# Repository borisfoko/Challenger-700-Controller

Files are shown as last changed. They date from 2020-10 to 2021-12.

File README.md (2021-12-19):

# Challenger-700-Controller
Dieses Projekt dient als demonstrator für den Einsatz von IoT Tracking und Zugangskontrolle Einheiten auf Flugzeugsschlepper (Challenger 700). Das Projekt umfasst:
- ein **Web frontend controller for Challenger 700**
- eine Ionic App controller für Challenger 700 Tractor - Robot
- **Arduino Sketchs** für den **Arduino Mega 2560** und **Arduino Uno** Controller des Challenger 700 Tractor-Robot
- 3D Zeichnungen mit Inventor sowie Zusammenbauten. Für 3D Bauteilen und stl kontaktieren Sie mich unter: fokoboris@gmail.com

Eine Demo der finallen Lösung in dem Video [Demo](assets/Demo.mp4) gesehen werden

## 1. Usecase Diagramm
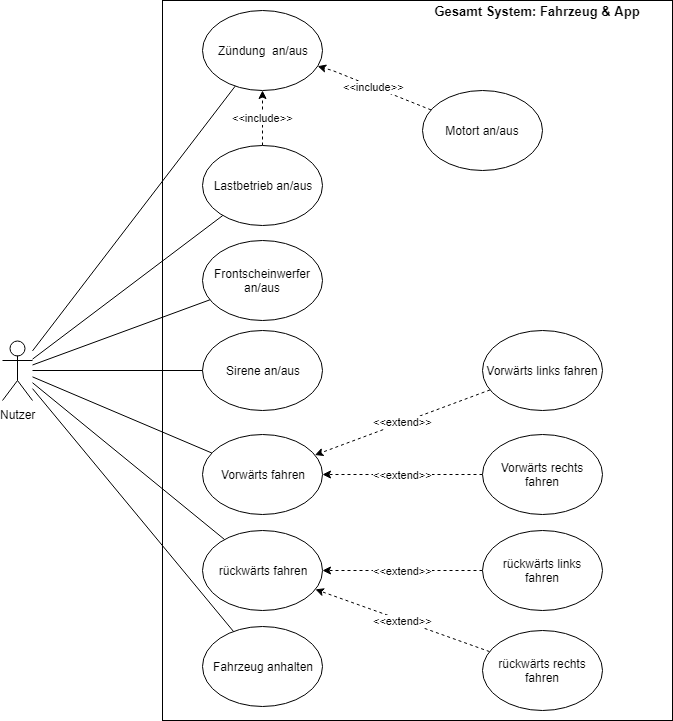
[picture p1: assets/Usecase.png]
Usecase


## 2. Komponent Diagramm
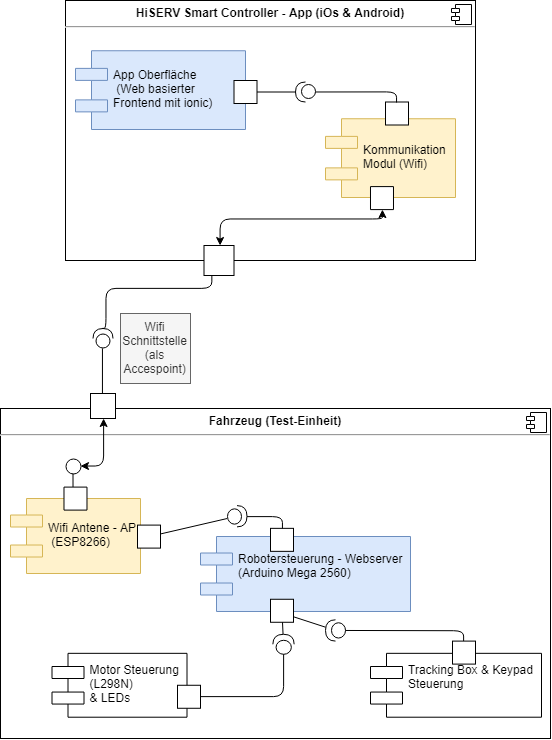
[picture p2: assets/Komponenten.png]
Komponents


## 3. Prozessüberblick: Fahrzeugsteuerung -  Workflow
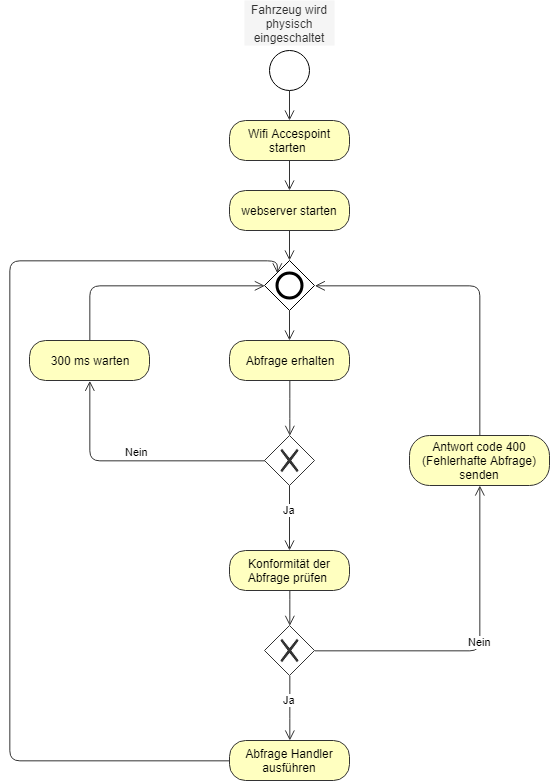
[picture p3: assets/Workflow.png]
Workflow


## 4. Tracking unit (IoT)
Trackunit Raw mit CAN-Bus (ME 500-4), Zubehör Dual ID Keypad
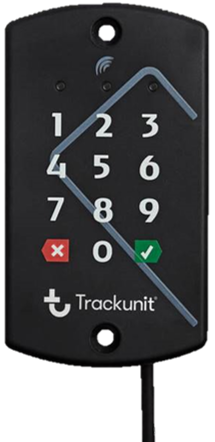
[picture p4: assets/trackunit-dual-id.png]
Trackunit device Dual ID
| Trackunit device Raw |  |
--- | ---|
|Tracking Raw ME 500 - 4: [Link](https://www.trackunit.com/hardware/raw-faq/)| Zubehör Dual ID Keypad: [Link](https://www.trackunit.com/hardware/accessories/trackunit-dualid-ii/)|

- Kommunikation über Wifi zwischen App und Test-Einheit (Fahrzeug) mit Hilfe eines ESP8266 
- Die Fahrzeugsteuerung soll mit Hilfe eines Arduino basierender Micro Controller umgesetzt  (Es besteht allerdings auch die Möglichkeit, diese mit einem Raspery Py 3 oder andere MicroController umzusetzen)
- Den Datenaustausch zwischen dem Raw 500 – 4 und den Trackunit – Gateway erfolgt über GSM und ist für dieses Projekt vorausgesetzt 

## 5. Schaltkreis: Fritzing Zeichnung

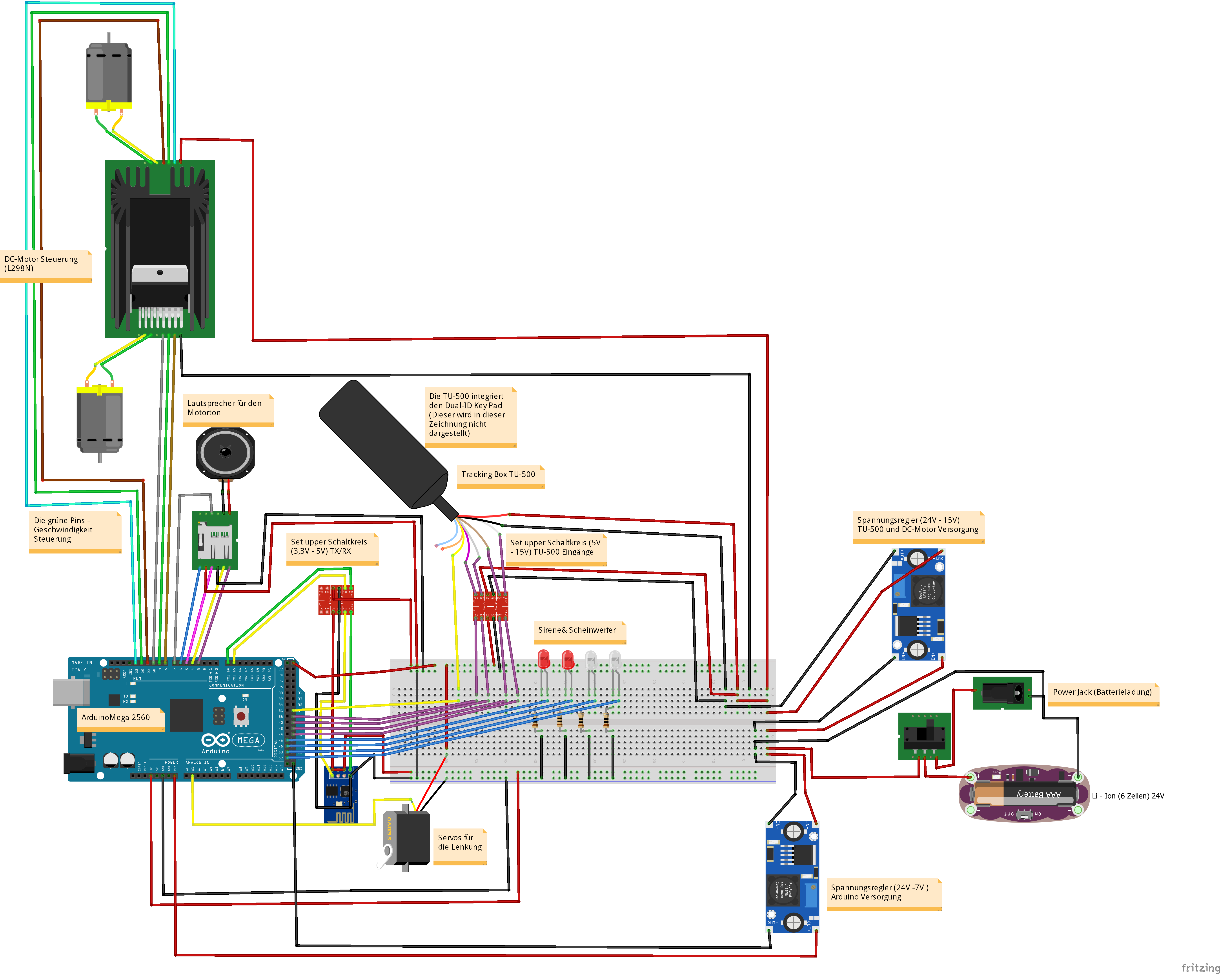
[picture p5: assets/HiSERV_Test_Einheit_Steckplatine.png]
Schaltplan Test Einheit


## 6. Realisierung

Die Realisierung erfolgt in zwei verschiedenen Schritten. Zuerst die Konstruktion und den 3D Druck von Bauteilen und anschließend die parallele Entwicklung der Fahrzeugsteuerung und der App (iOS, Android).

### 6.1. 3D Konstruktion
Insgesamt habe ich für die Test-Einheit 28 Bauteile gezeichnet. Hier werden vor allem Baugruppen und einige der wichtigsten Teile dargestellt

#### i. Chassis

Das Chassis ist aufgrund der maximale Drucklänge von 300 mm (3D Drucker bedingt) in zwei Teile gezeichnet worden:
•	Hauptteil: umfasst die Halter für die Vorder- und Hinterräder, sowie die Fläche für den Akku (Li-Ion Batterien), die Stützen für die Motoren und den Mikrocontroller (Arduino)
•	Das vordere Chassis: trägt die Kabine und wird an dem Hauptteil des Chassis angekoppelt.

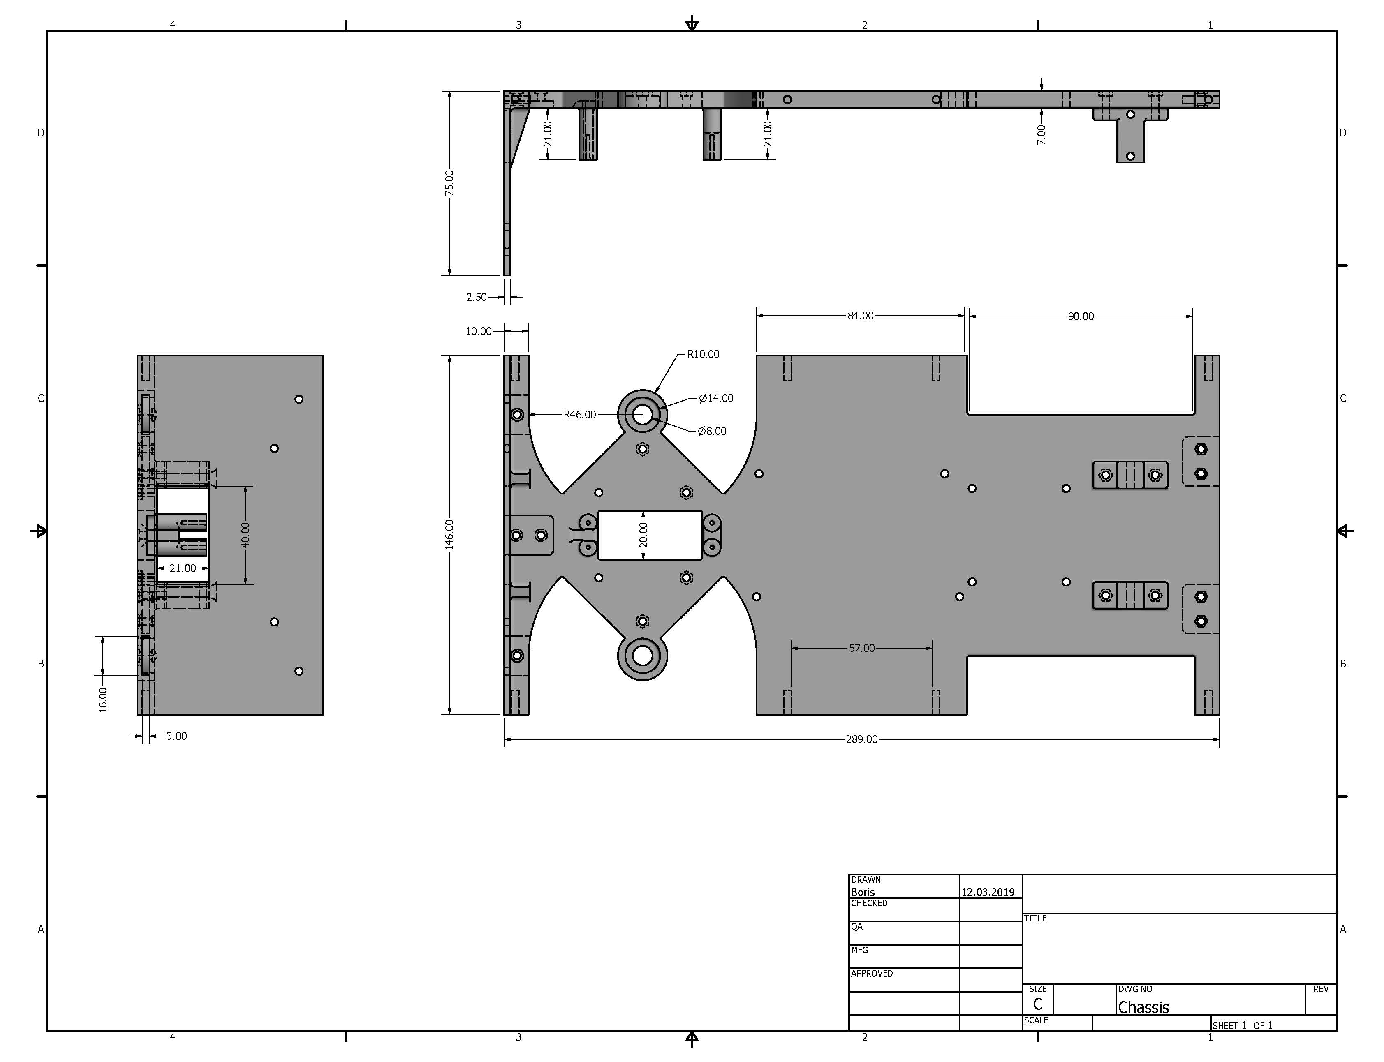
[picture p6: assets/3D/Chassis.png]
Chassis


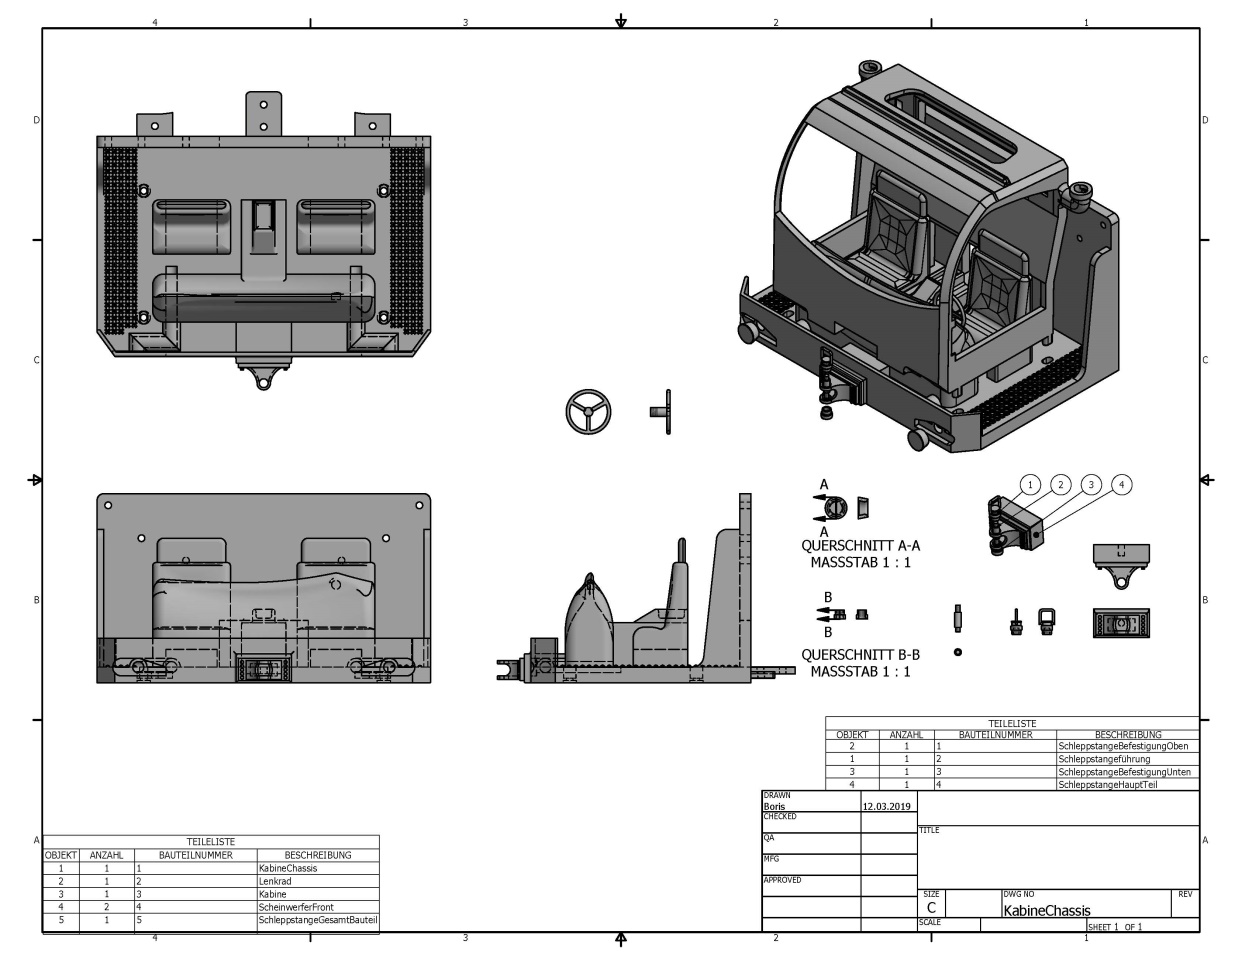
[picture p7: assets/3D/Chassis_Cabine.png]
Chassis & Cabine


#### ii.Kabine und Türen

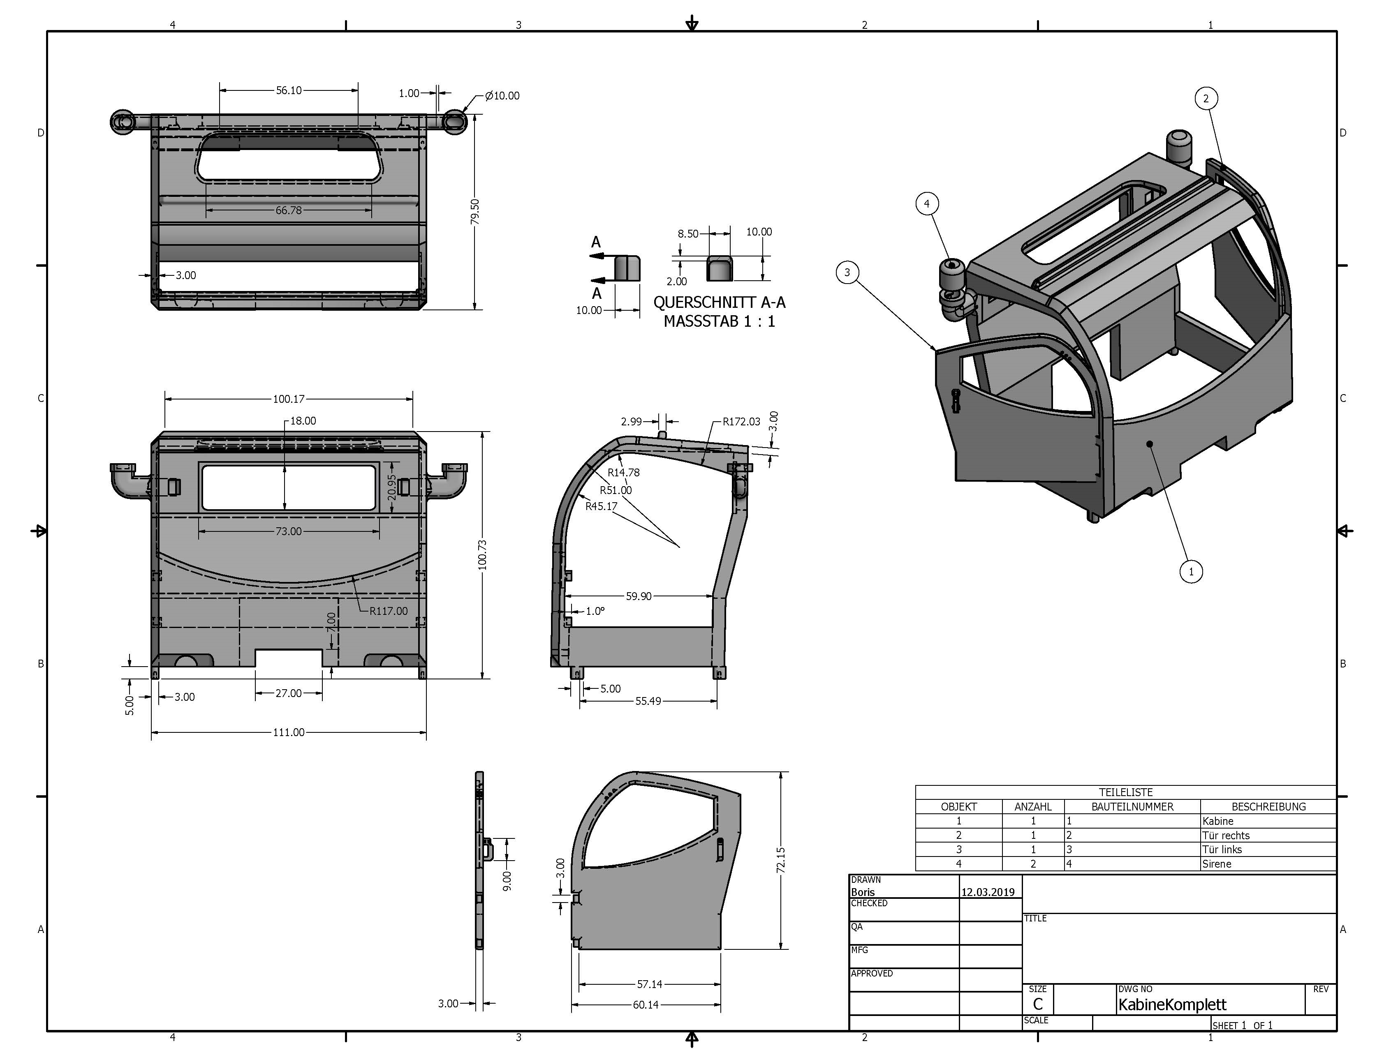
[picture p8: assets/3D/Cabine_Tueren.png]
Kabine & Türen


#### iii. Rad & Reifen

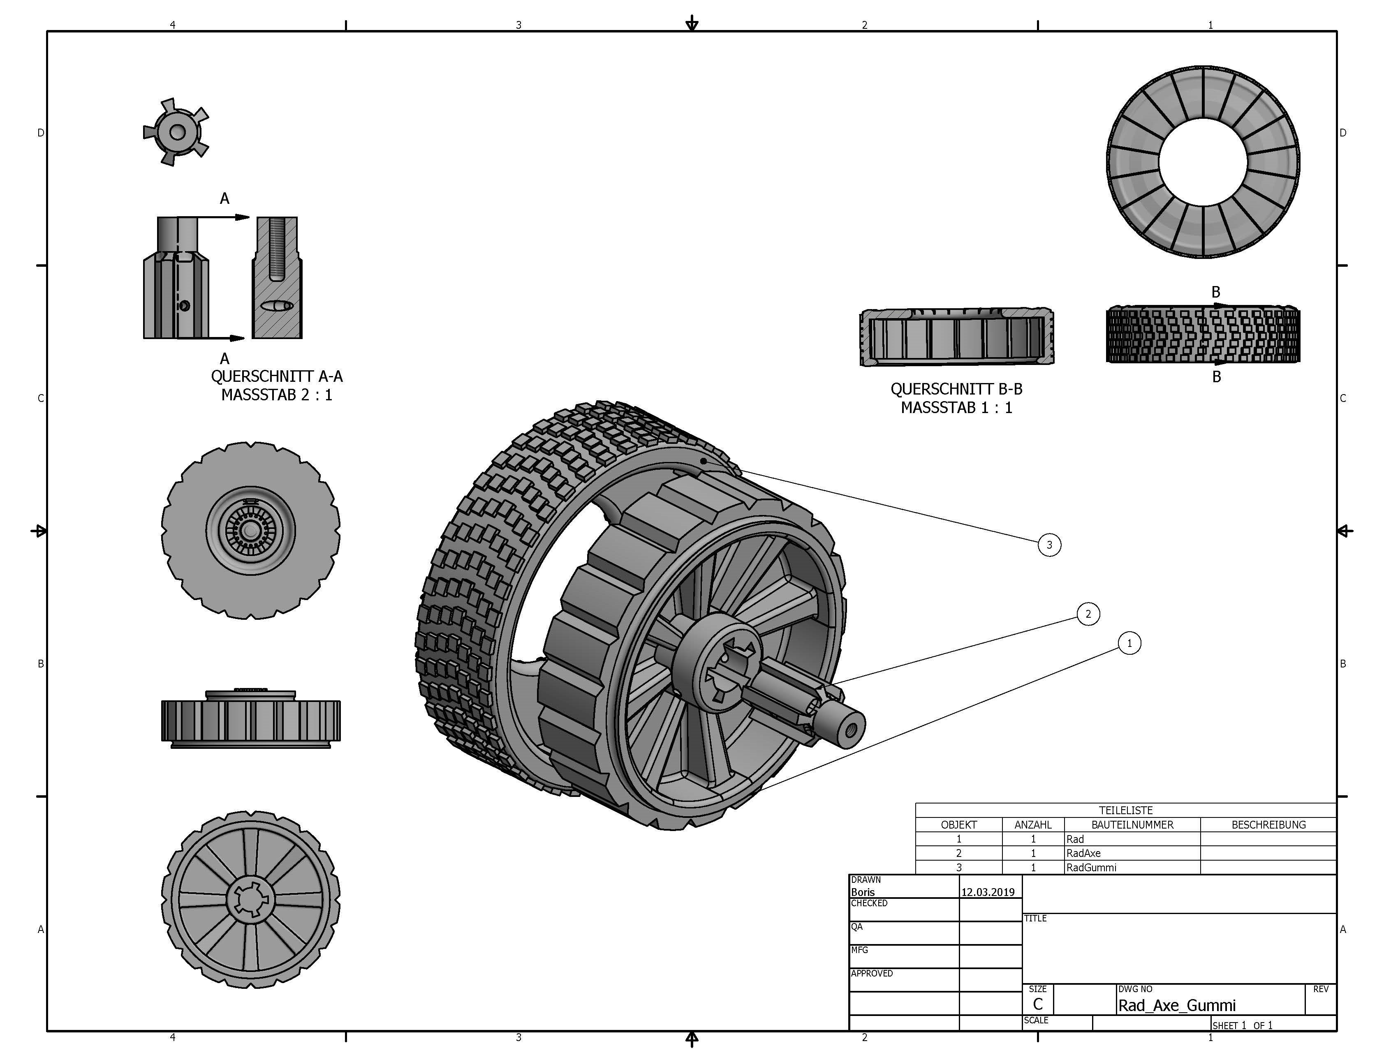
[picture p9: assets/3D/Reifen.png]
Rad & Reifen


#### iV. Zusammenbau

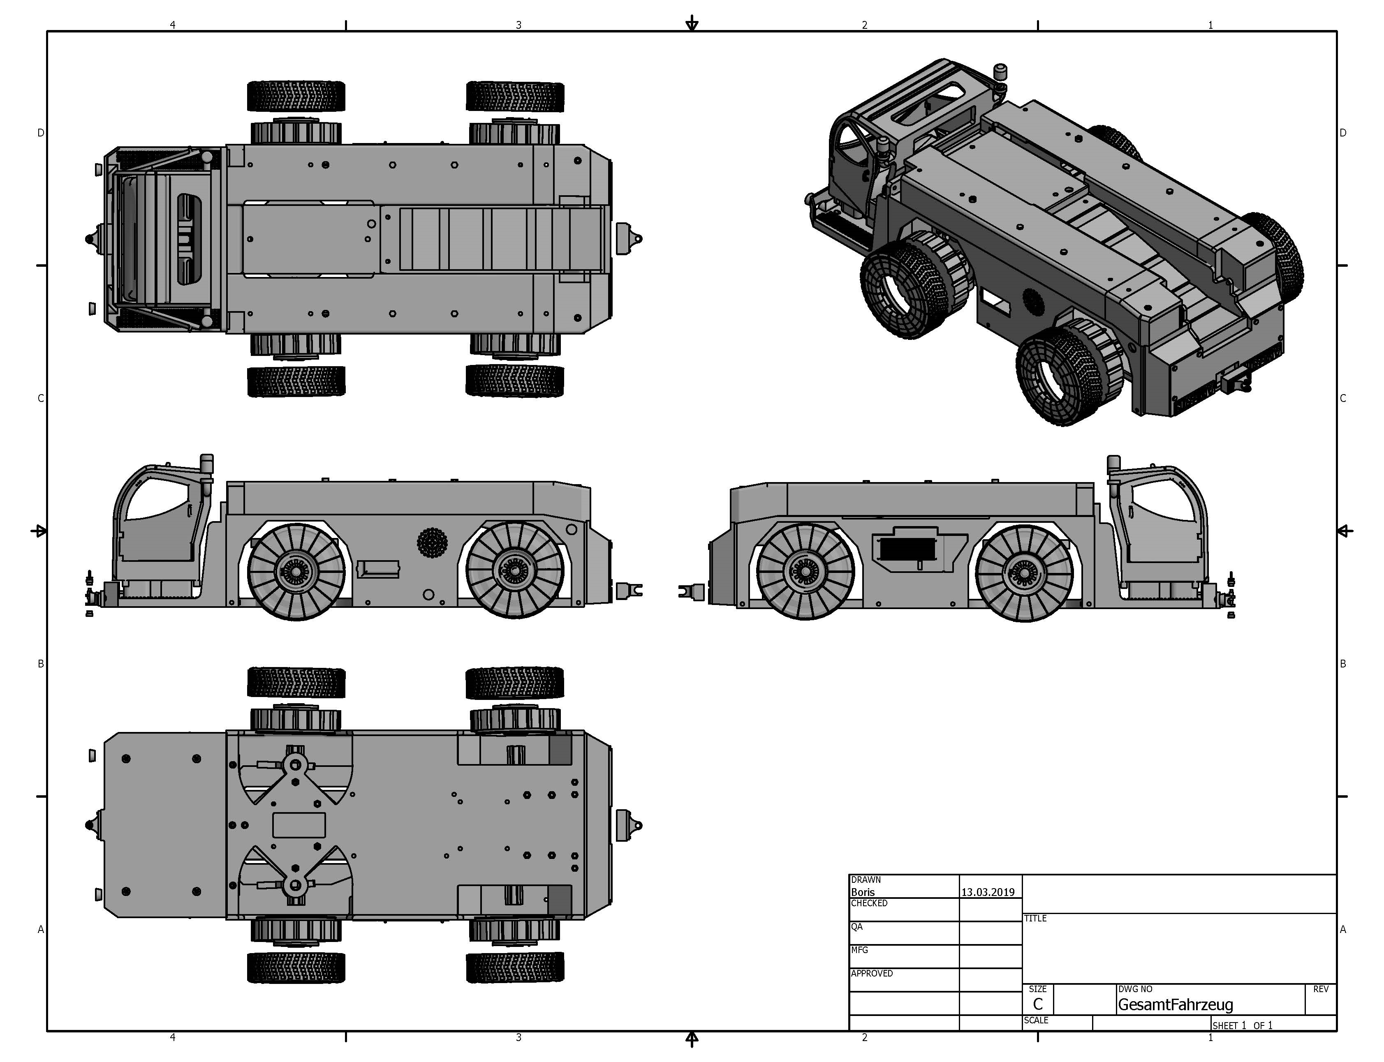
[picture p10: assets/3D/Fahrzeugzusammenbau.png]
Fahrzeugszusammenbau


### 6.3. Ergebnisse

#### i.	Fahrzeug: Ergebnis
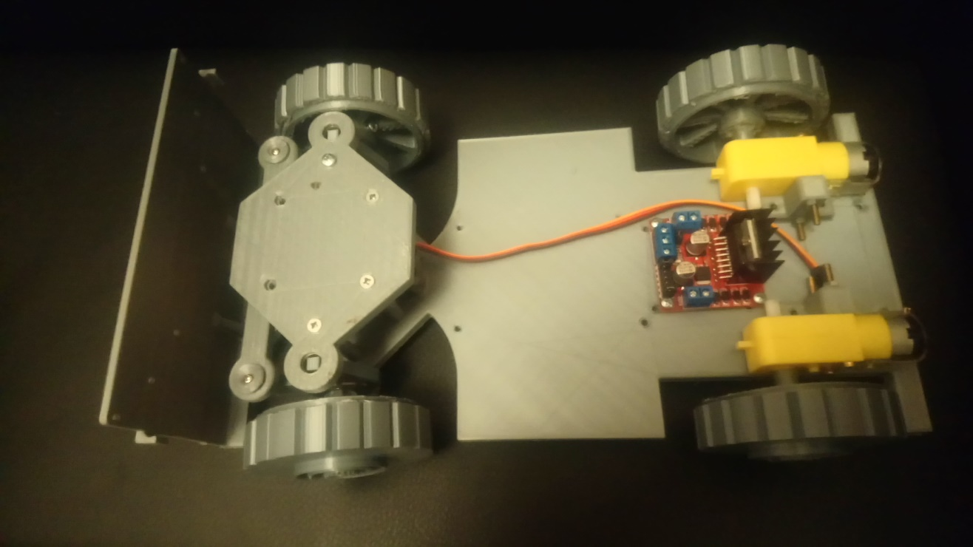
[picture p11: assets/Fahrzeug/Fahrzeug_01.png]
Fahrzeug_01


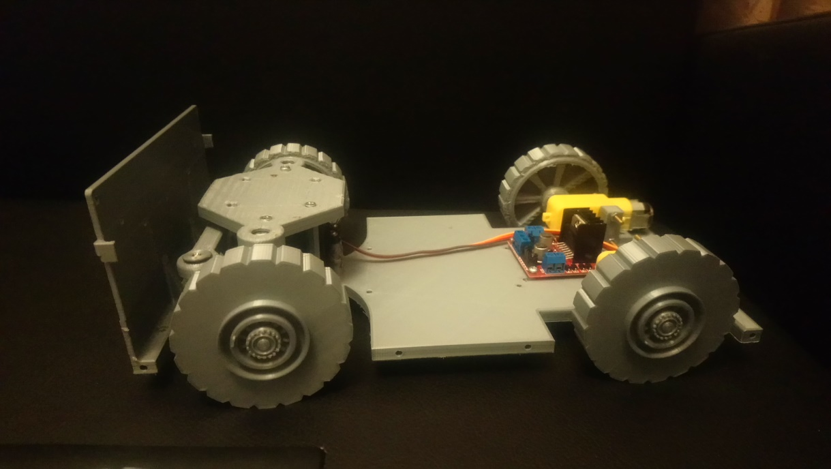
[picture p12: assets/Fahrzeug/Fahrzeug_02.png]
Fahrzeug_02

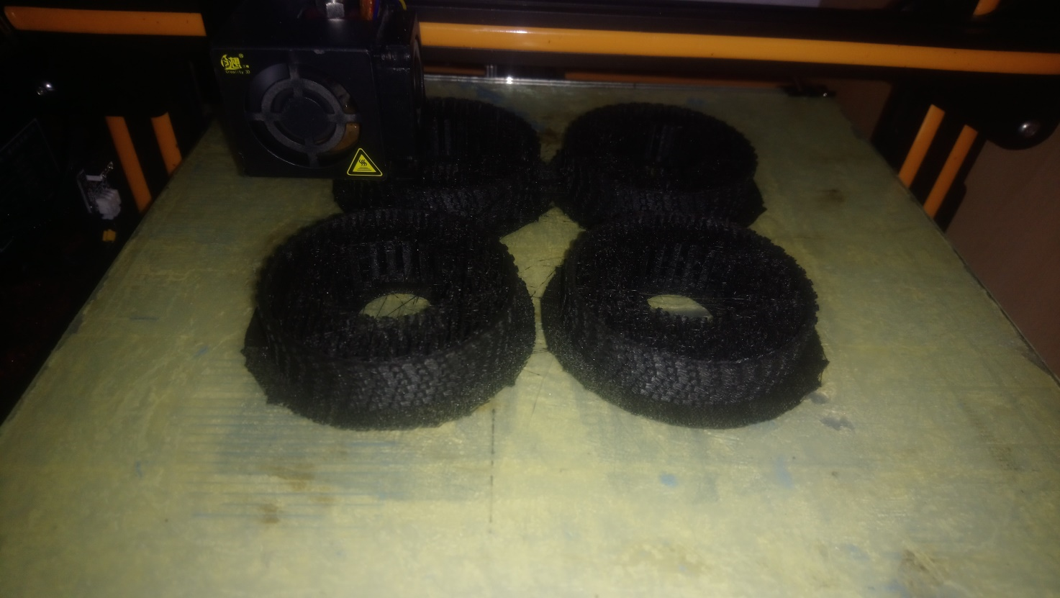
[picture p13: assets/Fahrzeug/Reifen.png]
Reifen

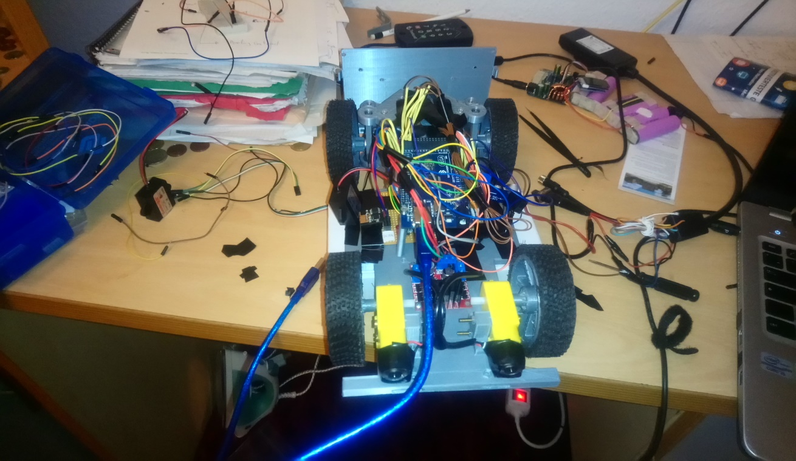
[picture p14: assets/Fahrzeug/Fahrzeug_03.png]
Fahrzeug_03

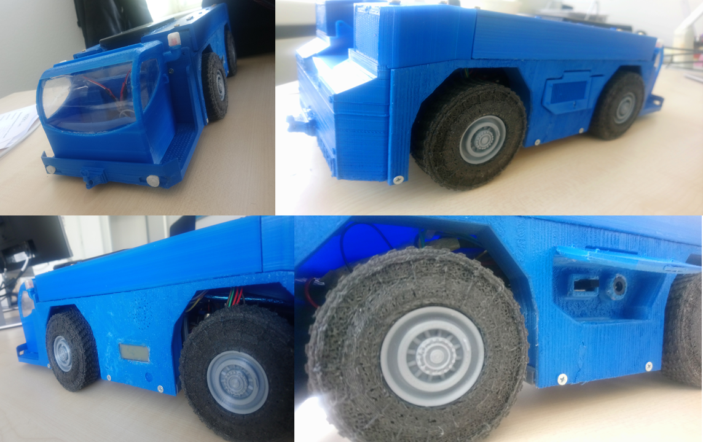
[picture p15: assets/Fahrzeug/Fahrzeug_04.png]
Fahrzeug_04

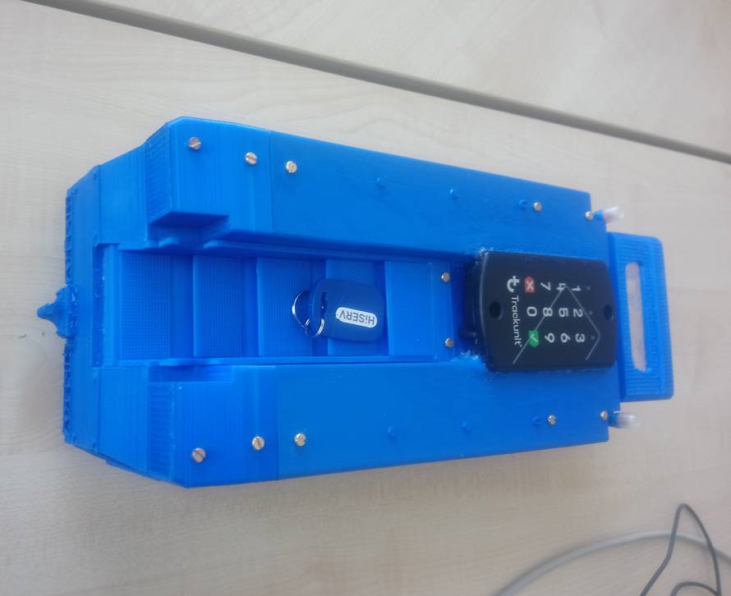
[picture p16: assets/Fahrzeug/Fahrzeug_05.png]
Fahrzeug_05


#### ii. Ionic App: Ergebnis
| Name | Image |
|---|--- |
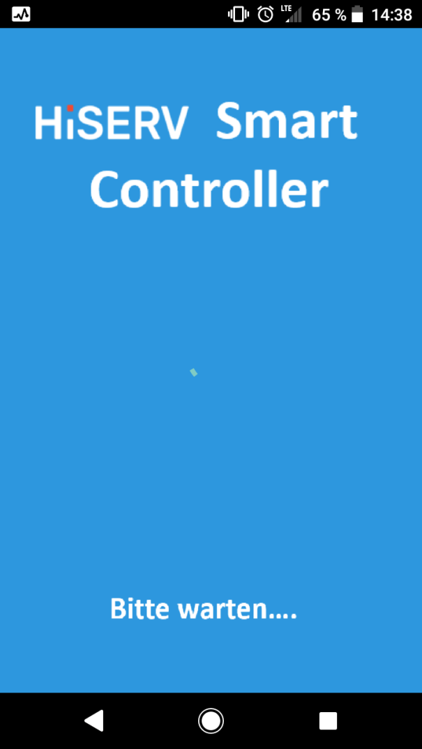
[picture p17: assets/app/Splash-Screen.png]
App Splash Screen
| App Splash Screen | |
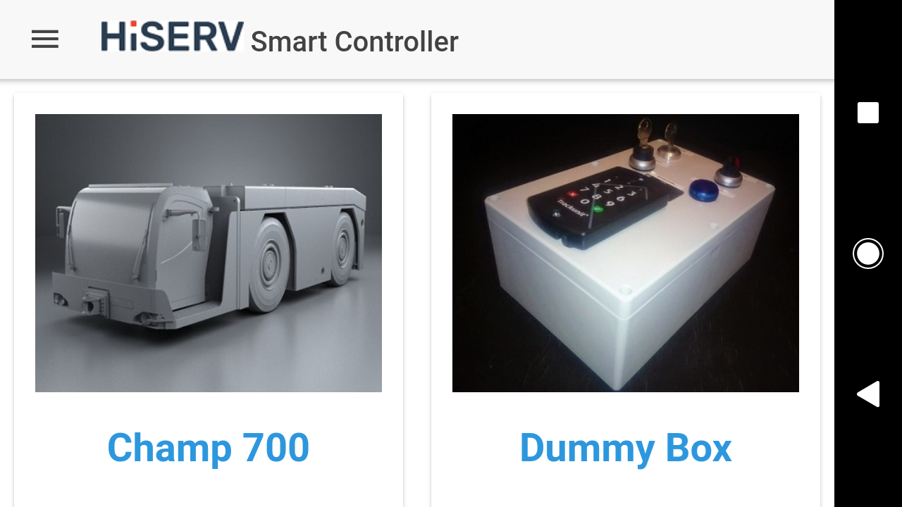
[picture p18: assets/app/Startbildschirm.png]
Startbildschirm
| Startbildschirm | |
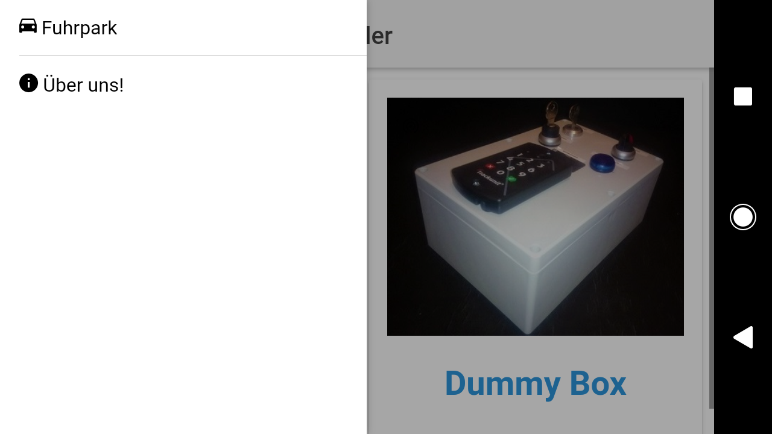
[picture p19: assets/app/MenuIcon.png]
Startbildschirm MenuIcon
| Startbildschirm MenuIcon | |
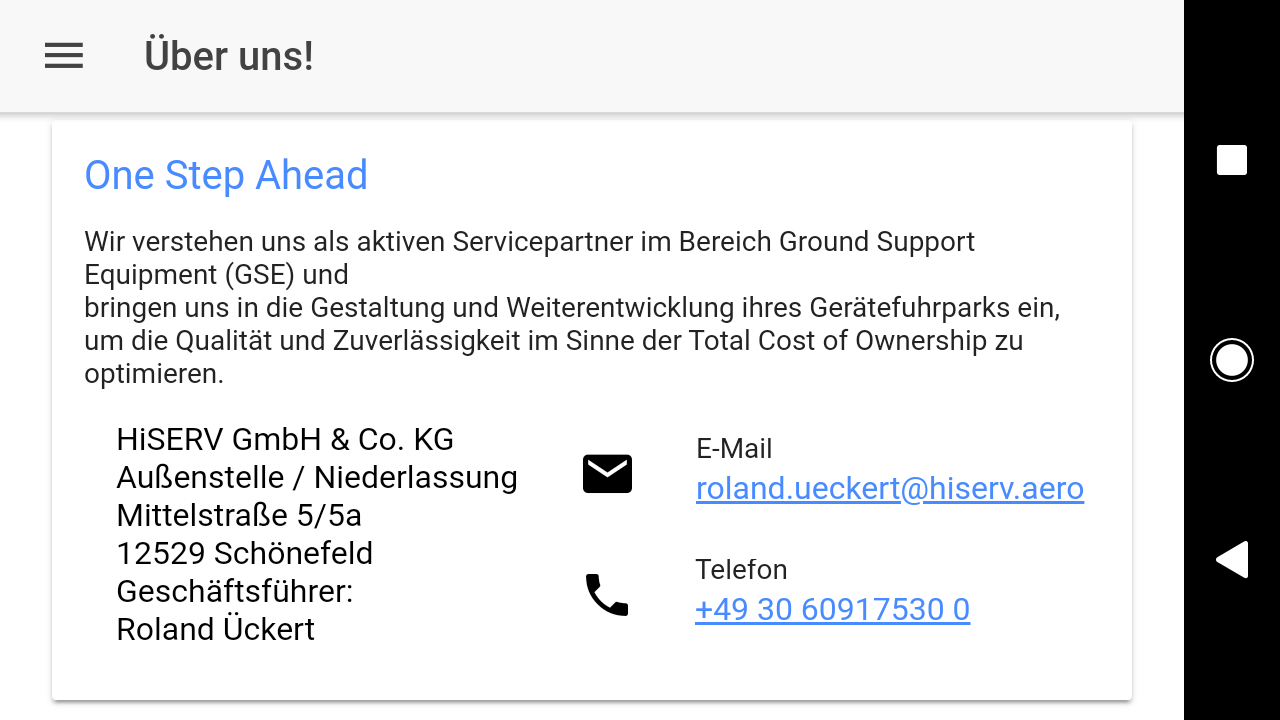
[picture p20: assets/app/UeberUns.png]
Über Uns
| Über Uns | |
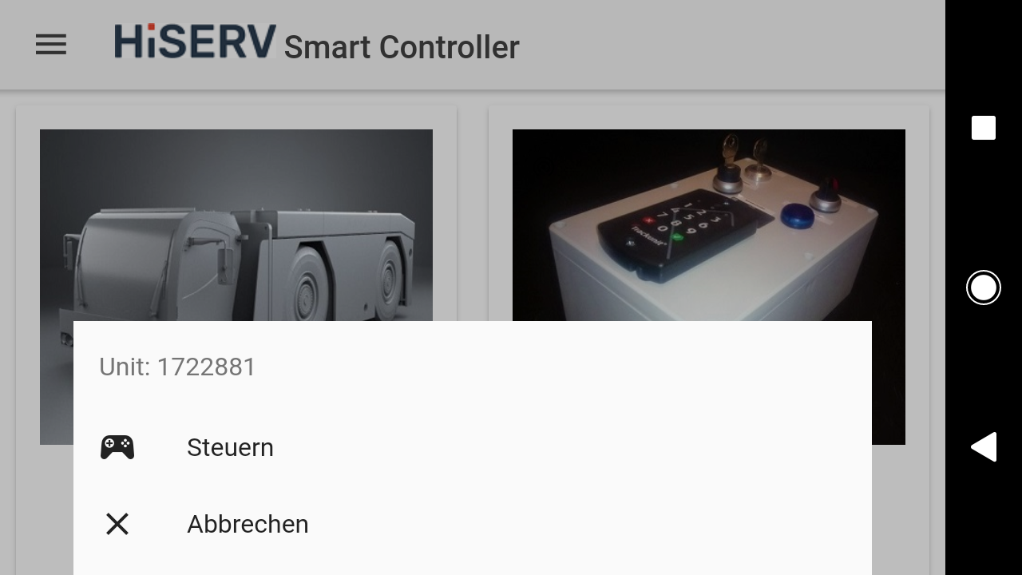
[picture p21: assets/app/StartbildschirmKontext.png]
StartbildschirmKontext
| Startbildschirm Kontext Menu | |
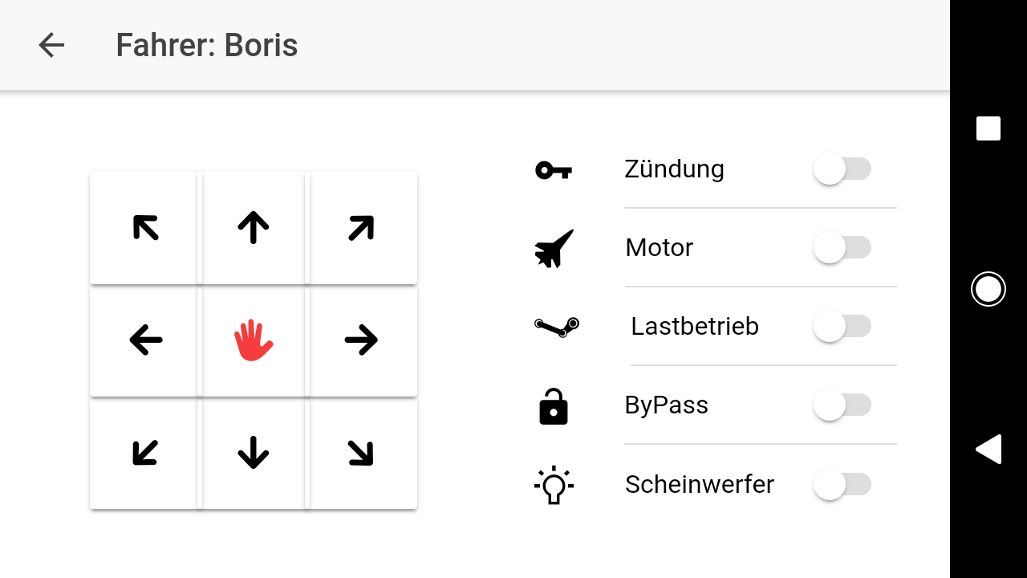
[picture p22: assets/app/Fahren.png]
Fahren - Steuerung
| Fahrzeugssteuerung | |

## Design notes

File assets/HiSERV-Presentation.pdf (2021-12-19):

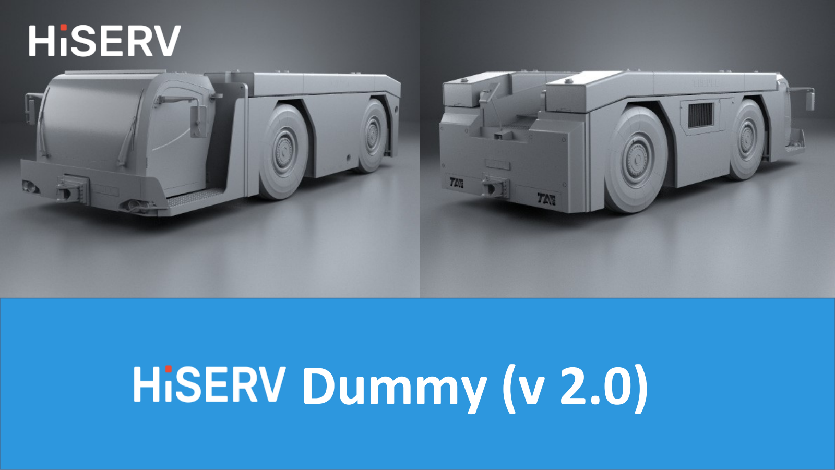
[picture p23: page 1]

# Dummy (v 2.0)

# Inhaltsverzeichnis

## ✓ Zielbeschreibung

## ✓ Planung

## ✓ Bauteile und Kostenschätzung

## ✓ Abnahme

Donnerstag, 11. Oktober 2018 | 2

# Zielbeschreibung

Nach der Entwicklung des HiSERV Dummy (v 1.0) zur Veranschaulichung der technischen Funktionalitäten von sowohl unseren Trackunit Raw (ME 5xxx) als auch die dazu gehörigen Zubehör wie den Keypad DualID II, habe ich mich mit diesem Projekt vorgenommen, eine fern steuerbare Erweiterung zu bauen. Diese soll alle Funktionalitäten der ersten Version und folgende zusätzliche Features implementieren: - das neue Modell soll eine Challenger 700 (Push-Back) ähnliche Makette sein

### - über WLAN steuerbar und durch eine Smartphone-App

### - Motor Brüllen beim Start und bei der Fahrt

### - iPhone & Android App: HiSERV Smart Controller

# Planung

## Planung über 11 Tage auf 10 Wochen verteilt, jeweils 8 Stunden am Tag

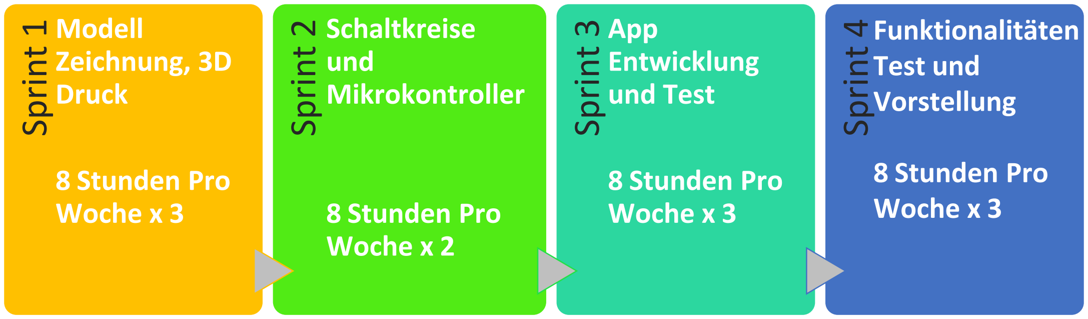
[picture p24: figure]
Sprint; 1Modell Zeichnung, 3D Druck; 8 Stunden Pro Woche x 3; 2Schaltkreise und Mikrokontroller; 8 Stunden Pro Woche x 2; 3App Entwicklung und Test; Funktionalitäten Test und Vorstellung

# Bauteile und Kostenschätzung

Name und Beschreibung | Menge | Einzelpreis(in Euro)
ME 5xxxx Trackunit Raw | 1 | (wird von der HiSERV zur Verfügung gestellt)
Keypad DualID II und die entsprechende Verkabelung dazu | 1 | (wird von der HiSERV zur Verfügung gestellt)
PLA Filament Rolle für die 3D Teile 1 kg | 2 | 50,00
Reifen Gummi und Räder Sätze | 5 | 6,00
Kugel Lager | 10 | 2,00
Schrauben und Muttern Sätze (Kasten) | 1 | 50,00
Arduino Mega 2560 (Microkontroller) | 1 | 50,00
ESP8266 E1 (Wifi Modul) | 1 | 10,00
Mainboard für Schaltkreise (zum Löten) | 1 | 10,00

# Bauteile und Kostenschätzung

Name und Beschreibung | Menge | Einzelpreis(in Euro)
Lötkolben Set | 1 | 50,00
Verkabelung Set Male & Female | 1 | 25,00
DC Motor (Microkontroller kompatibel) | 2 | 10,00
Servo Motor (Microstep kompatibel) | 2 | 10,00
Lautsprecher und Verstärker Amplifier für Arduino | 2 | 15,00
SD Karte Leser und 2Gb Micro SD Karte (Microkontroller) | 1 | 15,00
Wippschalter (Set von 10) | 1 | 10,00
Powerbank Litionite Falcon 24000mAh, 12V und DC-Hohlstecker | 1 | 80,00
Summe | 520,00 Euro

# Abnahme

## Die Abnahme erfolgt in etwa 2 ein halb Monate nach dem Test der bei

der Zielbeschreibung aufgelisteten Funktionalitäten.

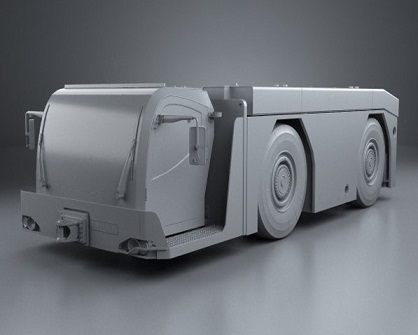
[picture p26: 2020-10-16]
Hiserv_Smart_Controller/src/assets/imgs/Dummy Champ 700.jpg

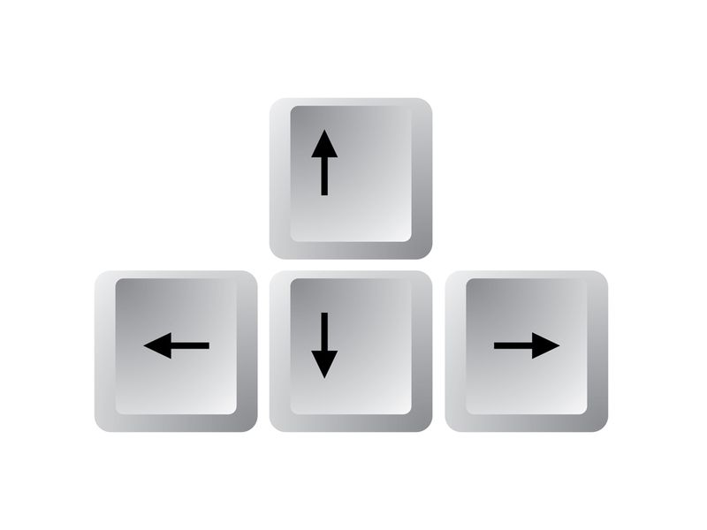
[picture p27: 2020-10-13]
Controller-Frontend/images/tastatur-pfeiltasten.jpg

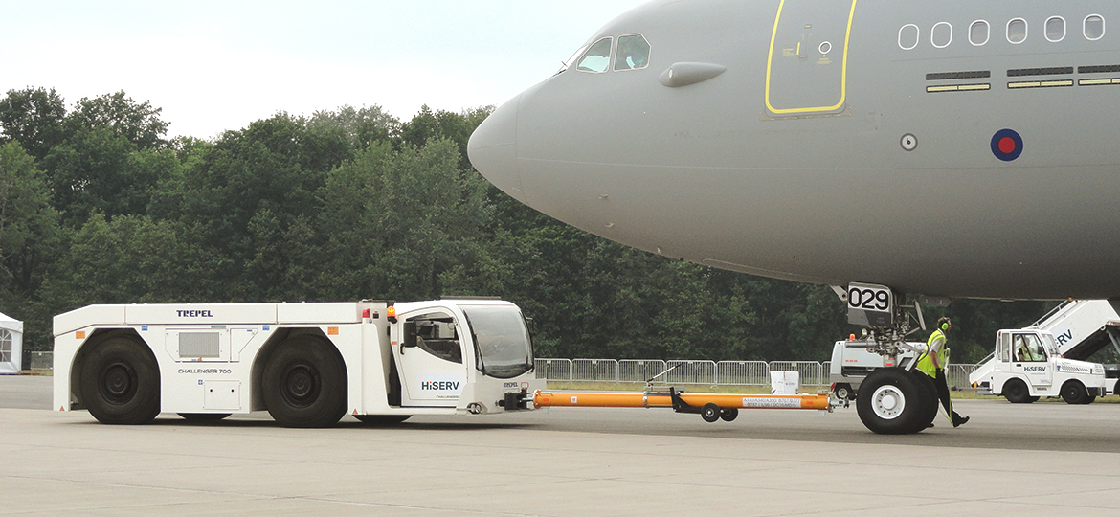
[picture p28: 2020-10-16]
Hiserv_Smart_Controller/src/assets/imgs/img-geraet-1.jpg

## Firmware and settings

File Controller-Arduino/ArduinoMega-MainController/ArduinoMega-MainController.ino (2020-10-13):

// < ---  ArduinoMega Mainboard Controller Programm --- >
// < --- von Boris Foko Kouti --- 

//Servos Bibliothek include
#include <Servo.h>

// Debug modus aus
#define DEBUG false

// Lenkung (Servos) Pin
#define ServosPin 3

// DC Motors Pins 8, 9, 10, 11
// Bei 8 & 10 auf HIGH und 9 & 11 auf LOW geht es vorwärts
// Bei 8 & 10 auf LOW und 9 & 11 auf HIGH geht es rückwärts
#define IN1 8
#define IN2 9
#define IN3 10
#define IN4 11
#define AEN1 4
#define AEN2 5

// Beleuchtung (LED) Pins 

// Front Scheinwerfer
#define FScheinWLED1 25
#define FScheinWLED2 26
// Sirene 
#define SireneLED1 24
#define SireneLED2 22

// Back Scheinwerfer
#define BScheinWLED1 23
#define BScheinWLED2 27
bool SireneOn = false;
bool FScheinWStatus = false;

// Trackunit Pins Output
#define BetriebsstundenPin 51
#define ZuendungPin 50
#define Batterieverbrauch 52
#define LastBSTPin 53

#define ZuendungSongPin 30
#define MotorSongPin 31

// Trackunit Pins Input
int SchluesselZugangPin = A8;
bool SchluesselZugangStatus = false;
bool BetriebsstundenStatus = false;
bool LastBSTStatus = false;
bool ByPassPin = false;
bool ZuendungOn = false;

// Servo Kontrolle Funktion Inizialisierung
Servo ServoLenkung;

void setup() {
  //Init Lautsprecher Modul
  //AudioPlayer.reset();
  // Init Lenkung Servo
  ServoLenkung.attach(ServosPin);
  ServoLenkungNull();
  // Init LED Pins
  pinMode(FScheinWLED1,OUTPUT);
  pinMode(FScheinWLED2,OUTPUT);
  pinMode(BScheinWLED1,OUTPUT);
  pinMode(BScheinWLED2,OUTPUT);
  pinMode(SireneLED1,OUTPUT);
  pinMode(SireneLED2,OUTPUT);

  digitalWrite(FScheinWLED1,HIGH);
  digitalWrite(FScheinWLED2,HIGH);
  digitalWrite(SireneLED1,HIGH);
  digitalWrite(SireneLED2,HIGH);
  delay(300);
  digitalWrite(BScheinWLED1,HIGH);
  digitalWrite(BScheinWLED2,HIGH);
  
  digitalWrite(FScheinWLED1,LOW);
  digitalWrite(FScheinWLED2,LOW);
  digitalWrite(SireneLED1,LOW);
  digitalWrite(SireneLED2,LOW);
  delay(300);
  digitalWrite(BScheinWLED1,LOW);
  digitalWrite(BScheinWLED2,LOW);

  //init Song interrupt Pins
  pinMode(ZuendungSongPin, OUTPUT);
  pinMode(MotorSongPin, OUTPUT);
  digitalWrite(ZuendungSongPin, LOW);
  digitalWrite(MotorSongPin, LOW);
  
  // DC Motors Init
  pinMode(AEN1, OUTPUT);
  pinMode(AEN2, OUTPUT);
  pinMode(IN1, OUTPUT);
  pinMode(IN2, OUTPUT);
  pinMode(IN3, OUTPUT);
  pinMode(IN4, OUTPUT);
  digitalWrite(IN1, LOW);
  digitalWrite(IN2, LOW);
  digitalWrite(IN3, LOW);
  digitalWrite(IN4, LOW);
  analogWrite(AEN1, 150);
  analogWrite(AEN2, 150);
  
  //Trackunit Dual Id Steuerung
  pinMode(BetriebsstundenPin, OUTPUT);
  pinMode(ZuendungPin, OUTPUT);
  pinMode(Batterieverbrauch, OUTPUT);
  pinMode(LastBSTPin, OUTPUT);
  digitalWrite(BetriebsstundenPin, LOW);
  digitalWrite(ZuendungPin, LOW);
  digitalWrite(Batterieverbrauch, LOW);
  digitalWrite(LastBSTPin, LOW);
  pinMode(48, OUTPUT);
  digitalWrite(48, HIGH);
  int value = 0;
  value = analogRead(SchluesselZugangPin);
  Serial.print("Value = ");
  Serial.println(value);
  // Init Serials für die Kommunikation
  Serial3.begin(115200);  // using serial 1 if you are using arduino LEO
  Serial.begin(9600);
  
  while (!Serial3) {
    ; // wait for serial port to connect. Needed for Leonardo only
  }
  delay(200);
  sendData("AT+RST\r\n",2000,DEBUG); // reset module
  Serial.println("Reseted");
  sendData("AT+CWMODE=2\r\n",1000,DEBUG); // configure as access point
  Serial.println("Configured");
  sendData("AT+CWSAP=\"HiSERV_CHAMP\",\"HiSERV_CHAMP\",5,3\r\n",1000,DEBUG);
  sendData("AT+CIFSR\r\n",1000,DEBUG); // get ip address //192.168.4.1
  sendData("AT+CIPMUX=1\r\n",1000,DEBUG); // configure for multiple connections
  sendData("AT+CIPSERVER=1,80\r\n",1000,DEBUG); // turn on server on port 80
  Serial.println("Server on");
}

void loop() {
  if(Serial3.available()) // prüf, ob eine Nachricht erhalten ist
  {
    if(Serial3.find("+IPD,"))
    {
      Serial3.find("?");
      String msg;
      msg = Serial3.readStringUntil(' ');
      //Serial.println("Message: " + msg);
      String command1 = msg.substring(0, 5);
      String command2 = msg.substring(6); 
      int value = 0;
      value = analogRead(SchluesselZugangPin);             
      if (DEBUG) 
      {
        Serial.println(command1);//Must print "robot"
        Serial.println(command2);//Must print "BYP" or "TES" or "ZUN" or "MOR" or "LAB" or "FWD" or "FWL" or "FWR" or "REV" or "REL" or "RER" or "STP" or "SWF" or "SIF"
        Serial.print("Value = ");
        Serial.println(value);
      }
      
      if(command2 == "TES"){
        //Test Connection
        Serial.println("Test");
        sirene();
        //sendMessage(1, 0);
      }
      if (command2 == "BYP"){
        if (!ByPassPin) {
           //ByPass
           ByPassPin = true;
           Serial.println("ByPass ON");
		       //sendMessage(1, 0);
        }else {
           //ByPass
           ByPassPin = false;
           Serial.println("ByPass OFF");
		       //sendMessage(2, 0);
        }  
      }
      if (value > 1000 && value < 1040){
            SchluesselZugangStatus = false;
      } 
      else if (value > 340 && value < 450) {
        SchluesselZugangStatus = true;
        Serial.println("KeyPad freigeschaltet");
      }
      if (ByPassPin || ZuendungOn || SchluesselZugangStatus){
        if (command2 == "ZUN"){
           digitalWrite(SireneLED1, HIGH);
           delay(200);
           digitalWrite(SireneLED1, LOW);
          if (!ZuendungOn){
             ZuendungOn = true;
             digitalWrite(ZuendungPin, HIGH);
             digitalWrite(ZuendungSongPin, HIGH);
             digitalWrite(MotorSongPin, LOW);
             Serial.println("Zuendung On");
			       //sendMessage(1, 0);
          }
          else {
            ZuendungOn = false;
            digitalWrite(ZuendungPin, LOW);
            digitalWrite(BetriebsstundenPin, LOW);
            digitalWrite(ZuendungSongPin, LOW);
            digitalWrite(MotorSongPin, LOW);
            Serial.println("Zuendung Off");
			      //sendMessage(2, 0);
          }
        }
        if (ZuendungOn){
           if (command2 == "MOR"){
              digitalWrite(SireneLED2, HIGH);
              delay(200);
              digitalWrite(SireneLED2, LOW);
              if (!BetriebsstundenStatus){
                digitalWrite(BetriebsstundenPin, HIGH);
                BetriebsstundenStatus = true;
                digitalWrite(ZuendungSongPin, LOW);
                digitalWrite(MotorSongPin, HIGH);
				        //sendMessage(1, 0);
              }
              else {
                digitalWrite(BetriebsstundenPin, LOW);
                BetriebsstundenStatus = false;
				        //sendMessage(2, 0);
              }      
           }
           if (command2 == "LAB"){
              SireneOn = !SireneOn; 
              if (!LastBSTStatus){
                digitalWrite(LastBSTPin, HIGH);
                LastBSTStatus = true;
				        //sendMessage(1, 0);
              }
              else {
                digitalWrite(LastBSTPin, LOW);
                LastBSTStatus = false;
				        //sendMessage(2, 0);
              }      
           }
           if (BetriebsstundenStatus){
              if (command2 == "STP"){
                 stoprobot();
              } 
              else if (command2 == "FWD"){
              forward();
              }
              else if (command2 == "FWR"){
                 rightForward();
              }
              else if (command2 == "LEF"){
                ServoLenkungLinks();
              }
              else if (command2 == "RIG"){
                ServoLenkungRechts();
              }
              else if (command2 == "FWL"){
                 leftForward();
              }
              else if (command2 == "REV"){
                 reverse();
              }
              else if (command2 == "RER"){
                 rightReverse();
              }
              else if (command2 == "REL"){
                 leftReverse();
              }
            }
         }
         if (command2 == "SWF"){
          if (!FScheinWStatus){
            //Scheinwerfer Vorne an
            digitalWrite(FScheinWLED1, HIGH);
            digitalWrite(FScheinWLED2, HIGH);
            FScheinWStatus = true;
          }else{
            FScheinWStatus = false;
            //Scheinwerfer Vorne aus
            digitalWrite(FScheinWLED1, LOW);
            digitalWrite(FScheinWLED2, LOW);
          }
         }
         if (command2 == "SIF"){
            //Sirene an/aus
            SireneOn = !SireneOn; 
         }
         if (SireneOn){
            sirene();
         } 
        }
      }
    }
    if (SireneOn){
       sirene();
    }
}

void _forward()
{
  //SONG_ON = true;
  digitalWrite(IN1, LOW);
  digitalWrite(IN2, HIGH);
  digitalWrite(IN3, LOW);
  digitalWrite(IN4, HIGH);
}

void forward()
{
  digitalWrite(ZuendungSongPin, LOW);
  digitalWrite(MotorSongPin, HIGH);
  ServoLenkungNull();
  _forward();
}

void _reverse()
{
  digitalWrite(IN1, HIGH);
  digitalWrite(IN2, LOW);
  digitalWrite(IN3, HIGH);
  digitalWrite(IN4, LOW);
}

void reverse()
{
  digitalWrite(ZuendungSongPin, LOW);
  digitalWrite(MotorSongPin, HIGH);
  ServoLenkungNull();
  _reverse();
}

void leftForward()
{
  digitalWrite(ZuendungSongPin, LOW);
  digitalWrite(MotorSongPin, HIGH);
  ServoLenkungLinks();
  _forward();
}

void rightForward()
{
  digitalWrite(ZuendungSongPin, LOW);
  digitalWrite(MotorSongPin, HIGH);
  ServoLenkungRechts();
  _forward();
}

void leftReverse()
{
  digitalWrite(ZuendungSongPin, LOW);
  digitalWrite(MotorSongPin, HIGH);
  ServoLenkungLinks();
  _reverse();
}

void rightReverse()
{
  digitalWrite(ZuendungSongPin, LOW);
  digitalWrite(MotorSongPin, HIGH);
  ServoLenkungRechts();
  _reverse();
}

void stoprobot()
{
  digitalWrite(IN1, LOW);
  digitalWrite(IN2, LOW);
  digitalWrite(IN3, LOW);
  digitalWrite(IN4, LOW);
}

void sirene(){
  digitalWrite(SireneLED1, HIGH);
  digitalWrite(SireneLED2, HIGH);
  //digitalWrite(BScheinWLED1, HIGH);
  //digitalWrite(BScheinWLED2, HIGH);
  delay(200);
  digitalWrite(SireneLED1, LOW);
  digitalWrite(SireneLED2, LOW);
  //digitalWrite(BScheinWLED1, LOW);
  //digitalWrite(BScheinWLED2, LOW);
  delay(100);
}

/*
 * Send Any Message
 */
void sendMessage(int message, int connectionId){
  // generate web page
  String webpage = String(message);
  String cipSend = "AT+CIPSEND=";
  cipSend += connectionId;
  cipSend += ",";
  cipSend +=webpage.length();
  cipSend +="\r\n";
  sendData(cipSend,1000,DEBUG);
  sendData(webpage,1000,DEBUG);
  
  // make close command
  String closeCommand = "AT+CIPCLOSE=";
  closeCommand+=connectionId; // append connection id
  closeCommand+="\r\n";
  
  sendData(closeCommand,1000,DEBUG); // close connection
}
 

/*
* Name: sendData
* Description: Function used to send data to ESP8266.
* Params: command - the data/command to send; timeout - the time to wait for a response; debug - print to Serial window?(true = yes, false = no)
* Returns: The response from the esp8266 (if there is a reponse)
*/
String sendData(String command, const int timeout, boolean debug)
{
  String response = "";
  
  Serial3.print(command); // send the read character to the esp8266
  
  long int time = millis();
  
  while( (time+timeout) > millis())
  {
    while(Serial3.available())
    {
    
    // The esp has data so display its output to the serial window
    char c = Serial3.read(); // read the next character.
    response+=c;
    }
  }
  
  if(debug)
  {
    Serial.print(response);
  }
  
  return response;
}

void ServoPosition(){
  Serial.print("Servos Position: ");
  Serial.println(ServoLenkung.read());
}

void ServoLenkungRechts(){
  int currentPos = ServoLenkung.read();
  while(currentPos > 25) {
    currentPos = currentPos - 5;
    ServoLenkung.write(currentPos);
    delay(50);
  }
}

void ServoLenkungLinks(){
  int currentPos = ServoLenkung.read();
  while(currentPos < 80) {
    currentPos = currentPos + 5;
    ServoLenkung.write(currentPos);
    delay(50);
  }
  Serial.println("Links");
}

void ServoLenkungNull(){
  int currentPos = ServoLenkung.read();
  if (currentPos != 45){
    if (currentPos > 45){
      while(currentPos > 45) {
        currentPos = currentPos - 5;
        ServoLenkung.write(currentPos);
        delay(50);
      }
    } else {
      while(currentPos < 45) {
        currentPos = currentPos + 5;
        ServoLenkung.write(currentPos);
        delay(50);
      }
    }
   }
}

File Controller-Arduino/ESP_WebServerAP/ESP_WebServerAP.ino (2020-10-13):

#include <ESP8266WiFi.h>
#include <WiFiClient.h>
#include <ESP8266WebServer.h>

#ifndef APSSID
#define APSSID "HiSERV_CHAMP"
#define APPSK  "HiSERV_CHAMP"
#endif

/* Set these to your desired credentials. */
const char *ssid = APSSID;
const char *password = APPSK;

ESP8266WebServer server(80);

/* Just a little test message.  Go to http://192.168.4.1 in a web browser
   connected to this access point to see it.
*/
void handleRoot() {
  server.send(200, "text/html", "<p>Du bist mit dem Champ 700 verbunden</p>");
}

void handleByPassAn() {
  server.send(200, "text/html", "<p>ByPass an</p>");
  Serial.write("?robot=BYN ");
}

void handleByPassAus() {
  server.send(200, "text/html", "<p>ByPass aus</p>");
  Serial.write("?robot=BYS ");
}

void handleZuendungAn() {
  server.send(200, "text/html", "<p>Zundung an</p>");
  Serial.write("?robot=ZUN ");
}

void handleZuendungAus() {
  server.send(200, "text/html", "<p>Zundung aus</p>");
  Serial.write("?robot=ZUS ");
}

void handleMotorAn() {
  server.send(200, "text/html", "<p>Motor an</p>");
  Serial.write("?robot=MON ");
}

void handleMotorAus() {
  server.send(200, "text/html", "<p>Motor aus</p>");
  Serial.write("?robot=MOS ");
}

void handleLastBetriebAn() {
  server.send(200, "text/html", "<p>Lastbetrieb an</p>");
  Serial.write("?robot=LAN ");
}

void handleLastBetriebAus() {
  server.send(200, "text/html", "<p>Lastbetrieb aus</p>");
  Serial.write("?robot=LAS ");
}

void handleForward() {
  server.send(200, "text/html", "<p>Nach vorne</p>");
  Serial.write("?robot=FWD ");
}

void handleForwardRight() {
  server.send(200, "text/html", "<p>Nach vorne rechts</p>");
  Serial.write("?robot=FWR ");
}

void handleForwardLeft() {
  server.send(200, "text/html", "<p>Nach vorne links</p>");
  Serial.write("?robot=FWL ");
}

void handleReverse() {
  server.send(200, "text/html", "<p>Zurueck</p>");
  Serial.write("?robot=REV ");
}

void handleReverseRecht() {
  server.send(200, "text/html", "<p>Zurueck rechts</p>");
  Serial.write("?robot=RER ");
}

void handleReverseLink() {
  server.send(200, "text/html", "<p>Zurueck links</p>");
  Serial.write("?robot=REL ");
}

void handleStop() {
  server.send(200, "text/html", "<p>Das Fahrzeug wird heruntergefahren</p>");
  Serial.write("?robot=STP ");
}

void handleFrontLigthAn() {
  server.send(200, "text/html", "<p>Scheinwerfer vorne an</p>");
  Serial.write("?robot=SWN");
}

void handleFrontLigthAus() {
  server.send(200, "text/html", "<p>Scheinwerfer vorne aus</p>");
  Serial.write("?robot=SWS ");
}

void handleSireneAn() {
  server.send(200, "text/html", "<p>Sirene an</p>");
  Serial.write("?robot=SIN ");
}

void handleSireneAus() {
  server.send(200, "text/html", "<p>Sirene aus</p>");
  Serial.write("?robot=SIS ");
}

void setup()
{
  delay(1000);
  Serial.begin(115200);
  Serial.println();

  Serial.print("Setting soft-AP ... ");
  WiFi.softAP(ssid, password);

  IPAddress myIP = WiFi.softAPIP();
  Serial.print("AP IP address: ");
  Serial.println(myIP);
  server.on("/", handleRoot);
  server.on("/BYN", handleByPassAn);
  server.on("/BYS", handleByPassAus);
  server.on("/ZUN", handleZuendungAn);
  server.on("/ZUS", handleZuendungAus);
  server.on("/MON", handleMotorAn);
  server.on("/MOS", handleMotorAus);
  server.on("/LAN", handleLastBetriebAn);
  server.on("/LAS", handleLastBetriebAus);
  server.on("/FWD", handleForward);
  server.on("/FWR", handleForwardRight);
  server.on("/FWL", handleForwardLeft);
  server.on("/REV", handleReverse);
  server.on("/REL", handleReverseLink);
  server.on("/RER", handleReverseRecht);
  server.on("/SWN", handleFrontLigthAn);
  server.on("/SWS", handleFrontLigthAus);
  server.on("/SIN", handleSireneAn);
  server.on("/SIS", handleSireneAus);
  server.on("/STP", handleStop);
  server.begin();
  Serial.println("HTTP server started");
}

void loop()
{
  server.handleClient();
}
